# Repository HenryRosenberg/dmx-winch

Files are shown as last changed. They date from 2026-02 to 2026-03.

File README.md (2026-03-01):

# DMX Winch Controller
ESP32-S3–based DMX512 winch controller for theater prop lifting. Supports web configuration, real-time position control, and comprehensive safety features.

**⚠️ For lifting props only. No humans below during movement.**

**These are not comprehensive instructions! This is a project overview**

Roxie Sign Winch v14

<br>

## Resources

| Resource | Link | Notes |
|---|---|---|
| Mechanical CAD Design | [Fusion360](https://a360.co/45cJdRQ) | Current, up-to-date design files |
| Project Overview Drawings | [Roxie Sign Winch Drawing v4](https://github.com/user-attachments/files/25563970/Roxie.Sign.Winch.Drawing.v4.pdf) | Outdated! For reference only. See CAD link for latest design. |
| Electrical Schematics | TBD | Not yet created. Refer to block diagram below |

## Controller Block Diagram
[High Resolution Linked Here](https://github.com/user-attachments/files/25567567/DMX.Winch.Block.Diagram.-.Google.Drawings.pdf)

DMX Winch Block Diagram

<br>

## Controller Parts List

controller_inside
<p align="center">
  
  
</p>

| Component | Part | Notes |
|---|---|---|
| MCU | [ESP32-S3-N16R8](https://www.aliexpress.us/item/3256808865544909.html) + [Carrier Board](https://www.aliexpress.us/item/3256807127113425.html) | Main controller |
| RS485 Transceiver (DMX) | [MAX-485 Module](https://www.aliexpress.us/item/3256809269106959.html) | DMX interface |
| Control PSU | [5V 2A (10W)](https://www.aliexpress.us/item/3256807161025414.html) | Powers MCU + other control circuitry |
| Motor Driver | [DM542T](https://www.omc-stepperonline.com/digital-stepper-driver-1-0-4-2a-20-50vdc-for-nema-17-23-24-stepper-motor-dm542t) | |
| Motor PSU | [48V 5.2A (250W)](https://www.omc-stepperonline.com/250w-48v-5-2a-115-230v-switching-power-supply-stepper-motor-cnc-router-kits-le-250-48) | Not auto-ranging |
| Brake Relay | [3V3 control, 24VDC 1A](https://www.aliexpress.us/item/3256807412441110.html) | |
| Brake PSU | [24V 1A (24W)](https://www.aliexpress.us/item/3256807161025414.html) | |
| Enclosure | [40×30×20 cm fiberglass](https://www.aliexpress.us/item/3256802803154446.html) | Easier to drill/file than steel |
| DIN Rail Mounts | See CAD files | 3D-printed mounts for MCU, relay, PSUs, MAX-485, driver |
| Misc. | WiFi antenna, AC/DC bus bars, PowerCon + 5-pin DMX connectors, panel-mount terminals, enclosure fans + filters, wiring | Source as available |

<br>

## Winch Parts List

Winch_on_floor

| Component | Part | Notes |
|---|---|---|
| Motor | [Dual Shaft NEMA 24 Stepper 4.2A 4Nm](https://www.omc-stepperonline.com/dual-shaft-nema-23-stepper-motor-4-2a-4nm-566oz-in-60x60x100mm-4-wires-24hs39-4204d) | Dual shaft required for brake |
| Electromagnetic Brake | [24V 2.0Nm for NEMA 23/24](https://www.omc-stepperonline.com/dc-electromagnetic-brake-24v-2-0nm-283oz-in-for-nema-23-24-stepper-motor-swb-03) | Failsafe/power loss holding |
| Gearbox | [10:1 Planetary](https://www.omc-stepperonline.com/eg-series-planetary-gearbox-gear-ratio-10-1-backlash-15-arc-min-for-8mm-shaft-nema-23-stepper-motor-eg23-g10-d8) | Low backlash, 8mm input directly from motor |
| Endstop | [ME-8166 Long Arm, N/O](https://www.aliexpress.us/item/3256804700433315.html) | Homing + safety |
| Lifting Drums | [400-12 Garage Door Cable Spools](https://www.amazon.com/dp/B09T5RJZRY) | 4.3" OD 1" ID (use 3d-printed 1/2 shaft adapters) |
| Bearings | [1/2" Bore Pillow Blocks](https://www.amazon.com/dp/B0C61FMWHY) | Self-centering |
| Slip Ring | [1/2" Bore, 6 wire, 10A](https://www.amazon.com/dp/B07XGPVKZK) | Power for light-up props |
| Shaft | [1/2" dia, 6' cold rolled](https://www.mcmaster.com/catalog/4437T11) | |
| Frame | [Engineering Drawing](https://github.com/user-attachments/files/25563765/Roxie.Sign.Winch.Drawing.for.construction.v3.pdf) | 2×4 construction + structural screws |
| Misc. | 14mm×12.7mm shaft coupler, Grade 12.9 hardware, lag bolts, motor mounts | |

<br>

## Engineering Calculations
[Original Calculation Spreadsheet](https://github.com/user-attachments/files/25564224/Chicago.Musical.Sign.Hoist.Calculations.xlsx)

### 1. Mass & Load Estimation (for ROXIE sign)
* **$A$** = $13.5 \text{ ft}^2$ (Area of 3/4" Plywood)
* **$\sigma$** = $2 \text{ lb/ft}^2$ (Density of Plywood)
* **$L$** = $16 \text{ ft}$ (Length of low profile steel Unistrut)
* **$\lambda$** = $0.8 \text{ lb/ft}$ (Linear Density of Low Profile Steel Unistrut)
* **$m_{\text{misc}}$** = $3 \text{ lb}$ (Bulbs & Wiring)

$$m_{\text{est}} = (A \cdot \sigma) + (L \cdot \lambda) + m_{\text{misc}}$$
$$m_{\text{est}} = (13.5 \cdot 2) + (16 \cdot 0.8) + 3 = \mathbf{42.8 \text{ lb}}$$
* **Design Load Limit ($m$):** $\mathbf{50 \text{ lb} \ (22.68 \text{ kg})}$ (before dynamic saftey factors)

---

### 2. Kinematics (Velocity & Gearing)
* **$\Delta y$** = $10 \text{ ft} \ (3.048 \text{ m})$ (Target Lifting Height)
* **$\Delta t$** = $15 \text{ s}$ (Target Lifting Time)
* **$d$** = $3 \text{ in} \ (0.0762 \text{ m})$ (Drum Diameter)
* **$N_{\text{motor}}$** = $500 \text{ RPM}$ (Target Stepper Speed for optimal torque)

**Required Linear Velocity:**
$$v = \frac{\Delta y}{\Delta t} = \frac{3.048}{15} = \mathbf{0.203 \text{ m/s}}$$

**Required Drum RPM:**
$$N_{\text{drum}} = \frac{60 \cdot v}{\pi \cdot d} = \frac{60 \cdot 0.203}{\pi \cdot 0.0762} = \mathbf{50.93 \text{ RPM}}$$

**Required Gear Ratio:**
$$i = \frac{N_{\text{motor}}}{N_{\text{drum}}} = \frac{500}{50.93} = \mathbf{9.82}$$
* **Selected Gearbox:** 10:1 Planetary

---

### 3. Dynamics (Torque & Power)
* **$SF$** = $2$ (Mechanical Safety Factor)
* **$g$** = $9.81 \text{ m/s}^2$
* **$\eta$** = $0.95$ (Gearbox Efficiency)

**Required Drum Torque:**
$$\tau_{\text{drum}} = (m \cdot g \cdot SF) \cdot \frac{d}{2}$$
$$\tau_{\text{drum}} = (22.68 \cdot 9.81 \cdot 2) \cdot \left(\frac{0.0762}{2}\right) = \mathbf{16.95 \text{ Nm}}$$

**Required Motor Torque:**
$$\tau_{\text{motor}} = \frac{\tau_{\text{drum}}}{i \cdot \eta} = \frac{16.95}{10 \cdot 0.95} = \mathbf{1.82 \text{ Nm}}$$
* **Selected Motor:** NEMA 24, Provides 2.2x torque headroom over required

**Required Mechanical Power:**
$$P = \tau_{\text{motor}} \cdot \left( \frac{N_{\text{motor}} \cdot 2\pi}{60} \right)$$
$$P = 1.82 \cdot \left( \frac{500 \cdot 2\pi}{60} \right) = \mathbf{95.16 \text{ W}}$$

---

### 4. Solid Mechanics (Shaft Deflection)
Checking to ensure the 2-foot driveshaft will not bend and bind the pillow block bearings under load. 

* **$E$** = $200 \text{ GPa} \ (2 \times 10^{11} \text{ Pa})$ (Young's Modulus of Steel)
* **$L_{\text{span}}$** = $2 \text{ ft} \ (0.6096 \text{ m})$ (Distance between bearings)
* **$d_{\text{shaft}}$** = $0.5 \text{ in} \ (0.0127 \text{ m})$ (Shaft Diameter)

**Area Moment of Inertia (Solid Circular Shaft):**
$$I = \frac{\pi \cdot d_{\text{shaft}}^4}{64} = \mathbf{1.28 \times 10^{-9} \text{ m}^4}$$

**Maximum Mid-Span Deflection (Worst-case point load assumption):**
$$\delta_{\text{max}} = \frac{F \cdot L_{\text{span}}^3}{48 \cdot E \cdot I}$$
$$\delta_{\text{max}} = \mathbf{0.29 \text{ mm}}$$
* **Conclusion:** Deflection is negligible; shaft is essentially rigid.

---
<br>

# Features

## Motion Control
- Smooth acceleration/deceleration
- Dual-core architecture (Core 0 dedicated to step generation)
- Non-blocking homing with configurable drop distance
- Tick-level position tracking

## DMX
- Single channel (0-255)
- Configurable address (1-512)
- 50ms dropout protection
- Optional auto-home on DMX=0
- Signal loss detection

## Safety
- Emergency stop (power cycle to clear)
- Limit switch monitoring
- Rope loop detection (E-STOP on downward limit hit)
- Auto-recovery (re-home on accidental upward limit hit)
- Electromagnetic brake control

## Web Interface
Screenshot 2026-02-27 at 1 08 30 PM
Access at http://DMXWinch.local if mDNS is supported on the network, else use the IP address assigned by DHCP.

- Real-time position display
- Stroke length, velocity, acceleration adjustment
- Brake modes (stop-on-zero, always-brake, motor-hold)
- Homing configuration
- Manual positioning for setup
- Persistent settings (survives power loss)
- Instant emergency stop button
- Build using the ESP-DASH library

## Status LED (NeoPixel, inside controll cabinet)

- 🔴 Red blink: E-STOP
- 🟣 Purple: Homing
- 🟢 Green: DMX active
- 🟡 Yellow blink: DMX signal lost
- 🟠 Orange: Manual mode
- 🔵 Cyan: Waiting for DMX
- 🔵 Blue: WiFi connecting

## DMX Mapping

- **0**: Auto-home (if enabled)
- **1**: Top (0")
- **255**: Bottomn (max stroke)
- Linear between 1-255

## Homing Sequence

1. Move up until the limit switch
2. Drop configured distance (default 2")
3. Set zero at the drop point
4. Repeat drop if still on limit switch

# Configuration

## Parameters
Edit WiFi in `main.cpp`:
```cpp
const char* ssid = "YourNetwork";
const char* password = "YourPassword";
```
Adjust other parameters in `main.cpp` as needed to match the physical setup.

# Safety Notes

## Automatic E-STOP triggers:
- Limit hit during downward motion (rope loop)
- Manual E-STOP pressed
- Position exceeds 1.5× stroke during homing

## Automatic recovery:
- Limit hit during upward motion (re-homes)
- DMX=0 received (if auto-home enabled)

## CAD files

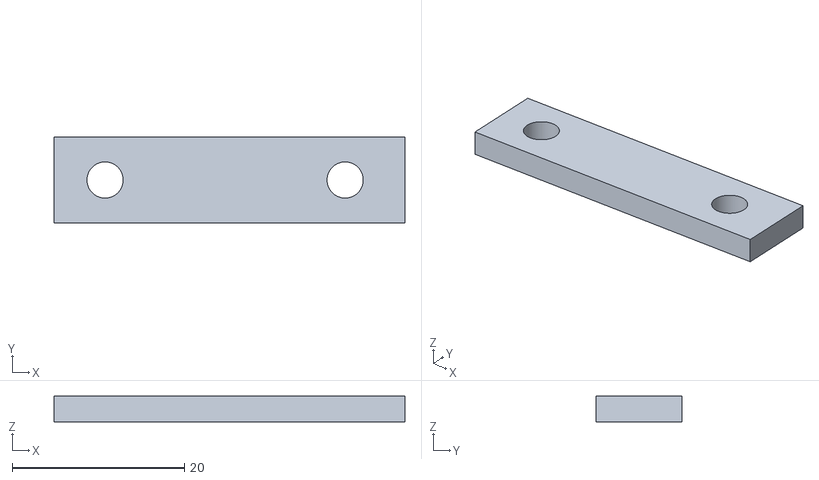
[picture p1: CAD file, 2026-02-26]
Additional STL Files/MAX485-DIN-Top.stl
40.8 x 10.0 x 3.00

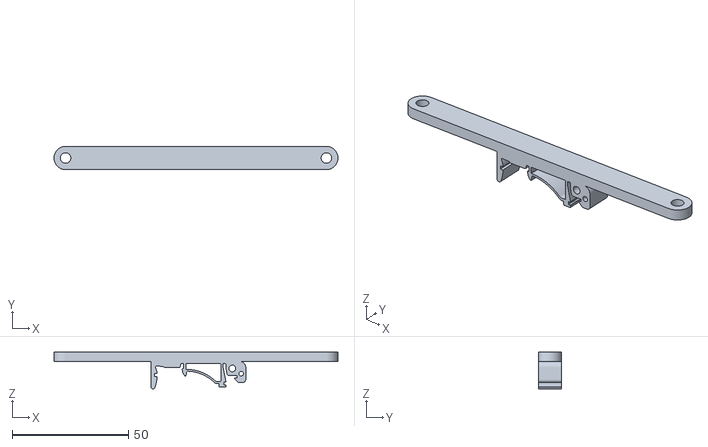
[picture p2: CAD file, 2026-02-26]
Additional STL Files/Driver-DIN-0.75Tolerance.stl
122.0 x 10.0 x 15.8

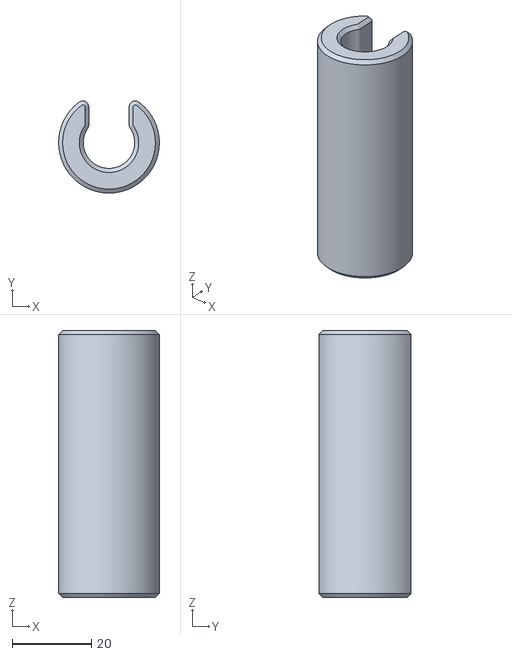
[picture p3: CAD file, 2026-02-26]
Additional STL Files/Garage Door Pulley to 1_2_ Shaft Adapter v1.stl
25.4 x 23.2 x 67.3

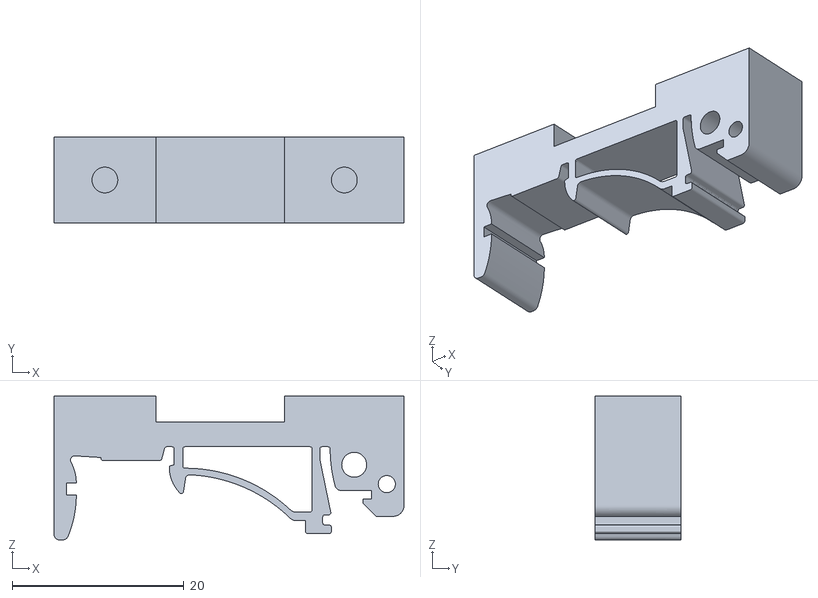
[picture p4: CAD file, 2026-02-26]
Additional STL Files/MAX485-DIN-BASE.stl
40.8 x 10.0 x 16.8

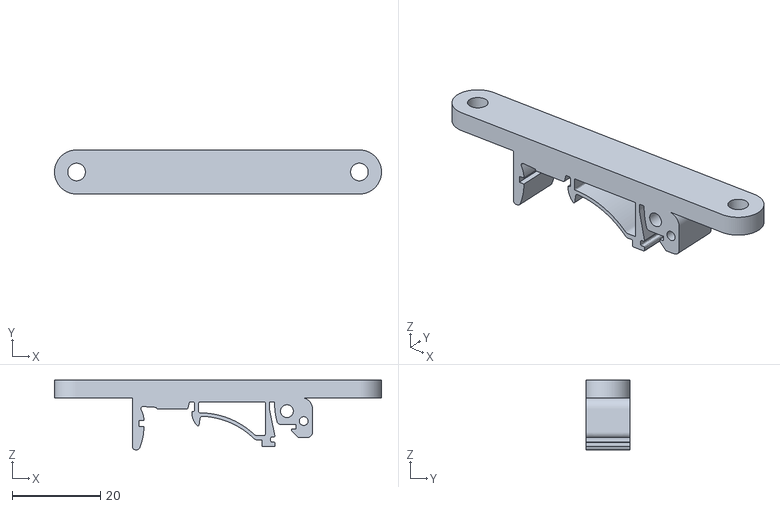
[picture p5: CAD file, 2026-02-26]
Additional STL Files/5V-PSU-DIN.stl
74.0 x 10.0 x 15.8

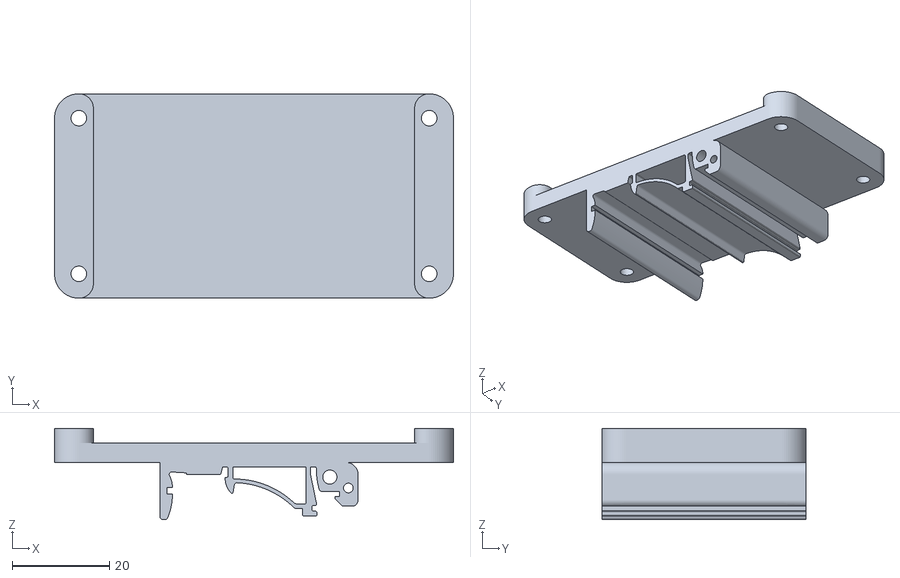
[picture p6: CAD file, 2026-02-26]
Additional STL Files/ESP-DIN.stl
82.0 x 42.0 x 18.8

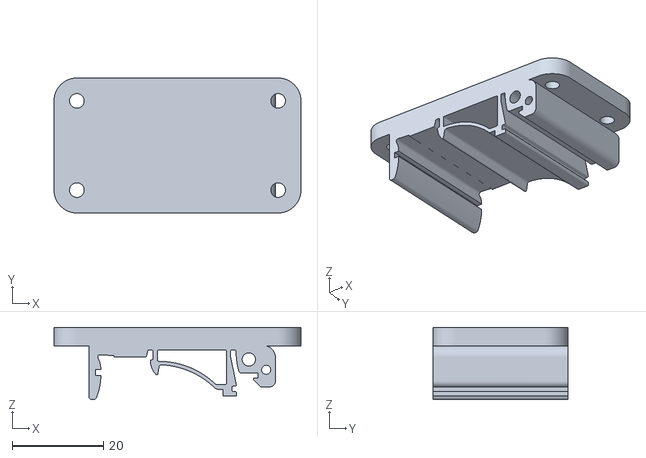
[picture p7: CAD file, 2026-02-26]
Additional STL Files/RELAY-DIN.stl
54.0 x 29.5 x 15.8

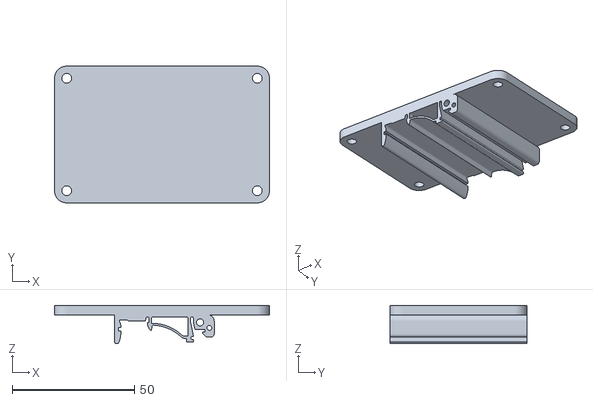
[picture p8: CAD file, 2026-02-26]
Additional STL Files/24V-PSU-DIN.stl
88.0 x 56.0 x 15.8

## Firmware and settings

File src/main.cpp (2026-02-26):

#include <Arduino.h>
#include <WiFi.h>
#include <ESPmDNS.h>
#include <AsyncTCP.h>
#include <ESPAsyncWebServer.h>
#include <ESPDash.h>
#include <AccelStepper.h>
#include <esp_dmx.h>
#include <Preferences.h>
#include <Adafruit_NeoPixel.h>

// WiFi Credentials <------------------------------------------------------- IMPORTANT: WiFi Credentials! <---------
const char* ssid = ""; // Network name
const char* password = ""; // Password
const char* hostname = "DMXWinch";

// DMX Dropout Protection: How long DMX must stay at 0 before acting on it (in milliseconds)
const unsigned long DMX_ZERO_DEBOUNCE_MS = 50; // Adjust this value to filter out momentary dropouts

// Hardware pinouts
const int PIN_STEPPER_PUL = 42;
const int PIN_STEPPER_DIR = 2;
const int PIN_STEPPER_ENA = 1;
const int PIN_STEPPER_BRAKE = 4;
const int PIN_LIMIT_SWITCH = 5;

const int PIN_DMX_RX = 11;  // RO on MAX485
const int PIN_DMX_TX = 14;  // DI on MAX485
const int PIN_DMX_EN = 12;  // DE and RE tied together on MAX485

const int TICKS_PER_REV = 3200;
const int GEAR_RATIO = 10;
const float DRUM_DIA_INCHES = 4.3;
const float INCH_TO_TICKS_RATIO = (GEAR_RATIO * TICKS_PER_REV) / (3.14159 * DRUM_DIA_INCHES);

int winchStrokeLength = 60; // in, Max extension of the winch
float dropDownAfterHoming = 2.0; // in, how much to lower the winch after hitting the endstop
bool autoHomeOnStartup = false; // Auto-home when powered on
bool autoHomeOnDMXZero = false; // Auto-home when DMX value is 0

bool enableDMXControl = true; // Can be disabled via webserver
bool brakeWhenNoMovement = false; // Can be enabled via webserver
bool brakeWhenAtZero = true; // Brake when at home position, can be disabled via webserver
bool isHoming = false; // Flag for non-blocking homing routine
bool homingDropping = false; // Track if we're in the drop-down phase of homing
bool eStopActive = false; // Emergency stop flag
bool dmxInitialized = false; // Track if DMX was successfully initialized

// DMX configuration
int dmxAddress = 1; // DMX start address (1-512)
const dmx_port_t dmxPort = DMX_NUM_1; // Port 0 on ESP32 is used for USB serial
unsigned long lastDmxPacket = 0;
bool dmxEverReceived = false;
const TickType_t DMX_POLL_TICKS = 0; // Non-blocking poll so loop stays responsive

// DMX dropout protection
unsigned long dmxZeroStartTime = 0; // When DMX first went to 0
bool dmxZeroConfirmed = false; // Has DMX been at 0 long enough?

// Persistent storage
Preferences preferences;

// NeoPixel setup
Adafruit_NeoPixel pixel(1, PIN_NEOPIXEL, NEO_GRB + NEO_KHZ800);

// NeoPixel status colors
#define COLOR_OFF             pixel.Color(0,   0,   0)
#define COLOR_WIFI_CONNECTING pixel.Color(0,   0,   100) // Blue
#define COLOR_WIFI_CONNECTED  pixel.Color(0,   100, 100) // Cyan
#define COLOR_DMX_ACTIVE      pixel.Color(0,   100, 0)   // Green
#define COLOR_MANUAL_MODE     pixel.Color(100, 50,  0)   // Orange
#define COLOR_ESTOP           pixel.Color(100, 0,   0)   // Red
#define COLOR_HOMING          pixel.Color(50,  0,   50)  // Purple
#define COLOR_DMX_LOST        pixel.Color(100, 100, 0)   // Yellow

// Use DRIVER mode for PUL/DIR stepper drivers
AccelStepper winchMotor(AccelStepper::DRIVER, PIN_STEPPER_PUL, PIN_STEPPER_DIR);

AsyncWebServer server(80); // Start Webserver
ESPDash dashboard(server); // Attach ESP-DASH to AsyncWebServer

// Webserver widgets
dash::SeparatorCard paramsSeparator(dashboard,              "Parameters:");
dash::SliderCard strokeLengthSlider(dashboard,              "Stroke Length (in)", 0, 240);
dash::SliderCard velocitySlider(dashboard,                  "Max Velocity (in/s)", 0, 20);
dash::SliderCard accelSlider(dashboard,                     "Acceleration (in/s^2)", 0, 50);
dash::ToggleButtonCard brakeWhenNoMovementButton(dashboard, "Brake when stopped?");
dash::ToggleButtonCard brakeWhenAtZeroButton(dashboard,     "Brake when DMX=0?");

dash::SeparatorCard homingSeparator(dashboard,         "Homing Settings:");
dash::SliderCard dropDownSlider(dashboard,             "Drop after homing (in)", 0, 12);
dash::ToggleButtonCard homeButton(dashboard,           "Home now");
dash::ToggleButtonCard autoHomeButton(dashboard,       "Home at startup?");
dash::ToggleButtonCard autoHomeOnZeroButton(dashboard, "Home when DMX=0?");

dash::SeparatorCard dmxSeparator(dashboard,       "DMX Settings:");
dash::ToggleButtonCard enableDMXButton(dashboard, "Enable DMX?");
dash::SliderCard dmxAddressSlider(dashboard,      "DMX Address", 1, 512);
dash::GenericCard dmxStatusCard(dashboard,        "DMX Status:");

dash::SeparatorCard toolsSeparator(dashboard, "Utilities:");
dash::ToggleButtonCard eStopButton(dashboard, "🛑 E-STOP 🛑");
dash::ToggleButtonCard resetButton(dashboard, "Hard Reset");

dash::SeparatorCard manualControlsSeparator(dashboard, "Manual Controls (DMX must be disabled):");
dash::ToggleButtonCard raiseButton(dashboard,          "Raise to 0");
dash::ToggleButtonCard lowerButton(dashboard,          "Lower to max");
dash::SliderCard goToPositionSlider(dashboard,         "Go to position", 0, 240);


void updateNeoPixel() {
  static unsigned long lastBlink = 0;
  static bool blinkState = false;
  
  // Blink every 500ms for certain states
  if(millis() - lastBlink > 500) {
    blinkState = !blinkState;
    lastBlink = millis();
  }
  
  // Priority order of status (highest priority first)
  if(eStopActive) {
    // ESTOP: Blinking red
    pixel.setPixelColor(0, blinkState ? COLOR_ESTOP : COLOR_OFF);
  }
  else if(isHoming) {
    // Homing: Solid purple
    pixel.setPixelColor(0, COLOR_HOMING);
  }
  else if(enableDMXControl && dmxEverReceived && (millis() - lastDmxPacket < 2000)) {
    // DMX Active: Solid green
    pixel.setPixelColor(0, COLOR_DMX_ACTIVE);
  }
  else if(enableDMXControl && dmxEverReceived && (millis() - lastDmxPacket >= 2000)) {
    // DMX Signal Lost: Blinking yellow
    pixel.setPixelColor(0, blinkState ? COLOR_DMX_LOST : COLOR_OFF);
  }
  else if(!enableDMXControl) {
    // Manual Mode: Solid orange
    pixel.setPixelColor(0, COLOR_MANUAL_MODE);
  }
  else if(!dmxInitialized) {
    // DMX init failed: Solid red (dim)
    pixel.setPixelColor(0, COLOR_ESTOP);
  }
  else {
    // WiFi Connected, waiting for DMX: Solid cyan
    pixel.setPixelColor(0, COLOR_WIFI_CONNECTED);
  }
  
  pixel.show();
}

// Motor task - runs on Core 0 for maximum smoothness
void motorTask(void* parameter) {
  // Disable watchdog for this task
  disableCore0WDT();
  
  while(true) {
    winchMotor.run();
  }
}

void setup() {
  Serial.begin(115200);
  Serial.println("\n\n=== DMX Winch Controller Starting ===");

  // Initialize NeoPixel
  pixel.begin();
  pixel.setBrightness(50); // 0-255
  pixel.setPixelColor(0, COLOR_WIFI_CONNECTING); // Blue while connecting
  pixel.show();

  pinMode(PIN_STEPPER_PUL,   OUTPUT);
  pinMode(PIN_STEPPER_DIR,   OUTPUT);
  pinMode(PIN_STEPPER_ENA,   OUTPUT);
  pinMode(PIN_STEPPER_BRAKE, OUTPUT);
  pinMode(PIN_LIMIT_SWITCH,  INPUT_PULLDOWN);
  
  digitalWrite(PIN_STEPPER_ENA, HIGH); // Disable the stepper driver on startup
  digitalWrite(PIN_STEPPER_BRAKE, LOW); // Engage brake on startup

  // Load persistent settings
  preferences.begin("winch", false); // Open in read/write mode
  winchStrokeLength = preferences.getInt("strokeLength", 60);
  brakeWhenNoMovement = preferences.getBool("brakeWhenStop", false);
  brakeWhenAtZero = preferences.getBool("brakeAtZero", true);
  dmxAddress = preferences.getInt("dmxAddress", 1);
  enableDMXControl = preferences.getBool("enableDMX", true);
  dropDownAfterHoming = preferences.getFloat("dropDown", 2.0);
  autoHomeOnStartup = preferences.getBool("autoHome", false);
  autoHomeOnDMXZero = preferences.getBool("autoHomeDMX0", false);
  
  Serial.println("Loaded persistent settings:");
  Serial.print("  Stroke Length: "); Serial.println(winchStrokeLength);
  Serial.print("  Drop After Homing: "); Serial.println(dropDownAfterHoming);
  Serial.print("  Auto Home (Startup): "); Serial.println(autoHomeOnStartup ? "Yes" : "No");
  Serial.print("  Auto Home (DMX=0): "); Serial.println(autoHomeOnDMXZero ? "Yes" : "No");
  Serial.print("  DMX Zero Debounce: "); Serial.print(DMX_ZERO_DEBOUNCE_MS); Serial.println(" ms");
  Serial.print("  DMX Address: "); Serial.println(dmxAddress);
  Serial.print("  Enable DMX: "); Serial.println(enableDMXControl ? "Yes" : "No");
  Serial.print("  INCH_TO_TICKS_RATIO: "); Serial.println(INCH_TO_TICKS_RATIO);

  // Configure DMX (esp_dmx returns bool: true = success)
  Serial.println("Initializing DMX...");
  dmx_config_t config = DMX_CONFIG_DEFAULT;
  dmx_personality_t personalities[] = {
    {1, "Winch Position"} // 1 channel personality
  };
  int personality_count = 1;

  if (dmx_driver_install(dmxPort, &config, personalities, personality_count)) {
    Serial.println("DMX driver installed");
    if (dmx_set_pin(dmxPort, PIN_DMX_TX, PIN_DMX_RX, PIN_DMX_EN)) {
      Serial.println("DMX pins configured");
      dmxInitialized = true;
      Serial.println("DMX initialized on port 1");
      Serial.print("Listening on DMX address: ");
      Serial.println(dmxAddress);
    } else {
      Serial.println("ERROR: Failed to set DMX pins");
    }
  } else {
    Serial.println("ERROR: Failed to install DMX driver");
  }

  // Connect to WiFi
  WiFi.mode(WIFI_STA);
  WiFi.begin(ssid, password);
  if (WiFi.waitForConnectResult() != WL_CONNECTED) {
      Serial.printf("WiFi Failed!\n");
      return;
  }
  Serial.print("IP Address: ");
  Serial.println(WiFi.localIP());
  Serial.print("RSSI: ");
  Serial.println(WiFi.RSSI());

  // mDNS allows the webpage to appear on http://DMXWinch.local
  if (!MDNS.begin(hostname)) {
    Serial.println("Error setting up MDNS");
  } else {
    Serial.print("mDNS started. Connect to: http://");
    Serial.print(hostname);
    Serial.println(".local");
  }

  WiFi.setAutoReconnect(true); // Automatically reconenct to WiFi if disconnected

  // Webserver callback configuration ---------------------------------------------
  enableDMXButton.onChange([](bool state){
    Serial.println(String("Enable DMX: ")+(state?"true":"false"));
    
    enableDMXControl = state;
    preferences.putBool("enableDMX", state);
    
    if (state) {
      dmxEverReceived = false;
      lastDmxPacket = 0;
      Serial.println("DMX state reset - ready for first packet");
    }

    enableDMXButton.setValue(state);
    dashboard.sendUpdates();
  });
  
  brakeWhenNoMovementButton.onChange([](bool state){
    Serial.println(String("Brake When No Movement: ")+(state?"true":"false"));
    
    brakeWhenNoMovement = state;
    preferences.putBool("brakeWhenStop", state);

    brakeWhenNoMovementButton.setValue(state);
    dashboard.sendUpdates();
  });

  brakeWhenAtZeroButton.onChange([](bool state){
    Serial.println(String("Brake When At Zero: ")+(state?"true":"false"));
    
    brakeWhenAtZero = state;
    preferences.putBool("brakeAtZero", state);

    brakeWhenAtZeroButton.setValue(state);
    dashboard.sendUpdates();
  });

  dropDownSlider.onChange([](int value){
    Serial.println("Drop Down Slider Triggered: "+String(value));
    
    dropDownAfterHoming = (float)value;
    preferences.putFloat("dropDown", dropDownAfterHoming);
    
    dropDownSlider.setValue(value);
    dashboard.sendUpdates();
  });

  autoHomeButton.onChange([](bool state){
    Serial.println(String("Auto Home on Startup: ")+(state?"true":"false"));
    
    autoHomeOnStartup = state;
    preferences.putBool("autoHome", state);

    autoHomeButton.setValue(state);
    dashboard.sendUpdates();
  });

  autoHomeOnZeroButton.onChange([](bool state){
    Serial.println(String("Auto Home on DMX=0: ")+(state?"true":"false"));
    
    autoHomeOnDMXZero = state;
    preferences.putBool("autoHomeDMX0", state);

    autoHomeOnZeroButton.setValue(state);
    dashboard.sendUpdates();
  });

  homeButton.onChange([](bool state){
    if(eStopActive) {
      Serial.println("ESTOP ACTIVE - Cannot home");
      return;
    }
    
    Serial.println("Home Button Triggered - Starting homing routine");
    
    if(state) {
      homingDropping = false; // Reset the homing state
      isHoming = true; // Start non-blocking homing routine
    }
  });

  eStopButton.onChange([](bool state){
    if(state) {
      Serial.println("🛑 EMERGENCY STOP ACTIVATED! 🛑");
      eStopActive = true;
      
      // Stop motor immediately
      winchMotor.stop();
      winchMotor.setCurrentPosition(winchMotor.currentPosition()); // Hold position
      
      // Engage brake and disable motor
      digitalWrite(PIN_STEPPER_BRAKE, LOW);
      digitalWrite(PIN_STEPPER_ENA, HIGH);
      
      // Disable DMX
      enableDMXControl = false;
      
      // Stop homing if active
      isHoming = false;
      
      eStopButton.setValue(true);
      dashboard.sendUpdates();
    }
  });

  resetButton.onChange([](bool state){
    Serial.println("Hard Reset Button Triggered");
    
    if(state) {
      // Engage brake and enable stepper driver during reset
      digitalWrite(PIN_STEPPER_BRAKE, LOW); // Enable motor brake
      digitalWrite(PIN_STEPPER_ENA, LOW); // Enable stepper driver
      
      delay(50); // Brief delay to ensure brake engages
      
      ESP.restart(); // Restart the MCU
    }
  });
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
void loop() {
  // Update NeoPixel status (quick, non-blocking)
  updateNeoPixel();
  
  // ESTOP overrides everything
  if(eStopActive) {
    digitalWrite(PIN_STEPPER_BRAKE, LOW);  // Brake engaged
    digitalWrite(PIN_STEPPER_ENA, HIGH);   // Motor disabled
    
    static unsigned long lastEStopMsg = 0;
    if(millis() - lastEStopMsg > 5000) {
      Serial.println("🛑 ESTOP ACTIVE 🛑 Cycle power to continue");
      if(WiFi.isConnected()) {
        dmxStatusCard.setValue("🛑 ESTOP ACTIVE 🛑");
        dashboard.sendUpdates();
      }
      lastEStopMsg = millis();
    }
    return;
  }

  // Limit switch: reset position if at home and motor thinks it's below zero
  bool limitSwitchTriggered = (analogReadMilliVolts(PIN_LIMIT_SWITCH) > 2500);
  if (limitSwitchTriggered && winchMotor.currentPosition() < 0 && !isHoming) {
    Serial.println("SAFETY: Limit switch hit while below zero - resetting to 0");
    winchMotor.setCurrentPosition(0);
    winchMotor.moveTo(0);
  }

  // Non-blocking homing routine
  if (isHoming) {
    digitalWrite(PIN_STEPPER_BRAKE, HIGH);
    digitalWrite(PIN_STEPPER_ENA, LOW);
    
    if (!homingDropping && limitSwitchTriggered) {
      // Step 1: Hit limit switch, now drop down
      Serial.print("Limit switch hit - dropping down ");
      Serial.print(dropDownAfterHoming);
      Serial.println("\"...");
      winchMotor.setCurrentPosition(0); // Current position is now zero
      winchMotor.moveTo(dropDownAfterHoming * INCH_TO_TICKS_RATIO); // Move down by dropDown amount
      homingDropping = true;
    } 
    else if (homingDropping && !winchMotor.isRunning()) {
      // Step 2: Finished dropping, check if still on limit switch
      if(limitSwitchTriggered) {
        // Still on limit switch after dropping - need to drop more!
        Serial.println("Still on limit switch after drop - dropping another " + String(dropDownAfterHoming) + "\"");
        winchMotor.setCurrentPosition(0);
        winchMotor.moveTo(dropDownAfterHoming * INCH_TO_TICKS_RATIO);
        // Stay in homingDropping mode
      } else {
        // Successfully dropped off limit switch - complete homing
        Serial.println("Drop complete - setting new zero");
        winchMotor.setCurrentPosition(0); // This dropped position is now the new zero
        winchMotor.moveTo(0); // Target is zero (stay here)
        isHoming = false;
        homingDropping = false;
        Serial.println("*** HOMING COMPLETE ***");
      }
    } 
    else if (!homingDropping) {
      // Step 0: Still searching for limit switch
      winchMotor.moveTo(-100000);
      
      // Safety check: if motor has moved too far, abort homing
      if(winchMotor.currentPosition() <= -1.5 * winchStrokeLength * INCH_TO_TICKS_RATIO) {
        isHoming = false;
        homingDropping = false;
        Serial.println("HOMING ABORTED - Extension limit reached without hitting limit switch");
        winchMotor.setCurrentPosition(0);
        winchMotor.moveTo(0);
      }
    }
    return;
  }

  // DMX Control - FAST, non-blocking poll
  static uint8_t lastDmxValue = 255;  // Track last value to avoid redundant moveTo calls
  if (enableDMXControl && dmxInitialized) {
    dmx_packet_t packet;
    size_t slotsNeeded = (size_t)(dmxAddress + 1);
    size_t received = dmx_receive_num(dmxPort, &packet, slotsNeeded, DMX_POLL_TICKS);

    if (received && !packet.err && packet.size > (size_t)dmxAddress) {
      int slotValue = dmx_read_slot(dmxPort, dmxAddress);
      if (slotValue >= 0) {
        uint8_t dmxValue = (uint8_t)slotValue;
        
        // DROPOUT PROTECTION: Special handling for DMX = 0
        if(dmxValue == 0) {
          if(dmxZeroStartTime == 0) {
            // First time we've seen 0 - start the timer
            dmxZeroStartTime = millis();
            dmxZeroConfirmed = false;
          } else if(!dmxZeroConfirmed && (millis() - dmxZeroStartTime >= DMX_ZERO_DEBOUNCE_MS)) {
            // DMX has been at 0 for long enough - confirm it
            dmxZeroConfirmed = true;
            Serial.print("DMX=0 confirmed after ");
            Serial.print(DMX_ZERO_DEBOUNCE_MS);
            Serial.println("ms");
          }
        } else {
          // DMX is not 0 - reset the zero detection
          dmxZeroStartTime = 0;
          dmxZeroConfirmed = false;
        }
        
        // Only update position if DMX value changed AND if it's 0, it must be confirmed
        if(dmxValue != lastDmxValue) {
          if (!dmxEverReceived) {
            Serial.println("*** FIRST DMX PACKET RECEIVED! ***");
            dmxEverReceived = true;
          }
          
          // DMX = 0: Only act on it if confirmed (not a momentary dropout)
          if(dmxValue == 0) {
            if(dmxZeroConfirmed && autoHomeOnDMXZero) {
              Serial.println("DMX: Ch" + String(dmxAddress) + " = 0 (confirmed) → Starting auto-home");
              homingDropping = false; // Reset the homing state
              isHoming = true;
              lastDmxValue = dmxValue; // Update so we don't repeat
            }
            // If not confirmed yet, don't update lastDmxValue - wait for confirmation
          }
          else {
            // DMX 1-255: Map to stroke length (1 goes to top, 255 goes to max)
            int targetPosition = map(dmxValue, 1, 255, 0, winchStrokeLength);
            Serial.print("DMX: Ch");
            Serial.print(dmxAddress);
            Serial.print(" = ");
            Serial.print(dmxValue);
            Serial.print(" → Moving to ");
            Serial.print(targetPosition);
            Serial.println("\"");
            
            winchMotor.moveTo(targetPosition * INCH_TO_TICKS_RATIO);
            lastDmxValue = dmxValue;
          }
        }
        
        lastDmxPacket = millis();
      }
    }
  }


  // Brake and motor enable control  
  if(winchMotor.isRunning()) {
    digitalWrite(PIN_STEPPER_BRAKE, HIGH);
    digitalWrite(PIN_STEPPER_ENA, LOW);
  }
  else if(brakeWhenAtZero && winchMotor.currentPosition() == 0) {
    digitalWrite(PIN_STEPPER_BRAKE, LOW);
    digitalWrite(PIN_STEPPER_ENA, HIGH);
  }
  else if(brakeWhenNoMovement) {
    digitalWrite(PIN_STEPPER_BRAKE, LOW);
    digitalWrite(PIN_STEPPER_ENA, HIGH);
  }
  else {
    digitalWrite(PIN_STEPPER_BRAKE, HIGH);
    digitalWrite(PIN_STEPPER_ENA, LOW);
  }

  // Limit switch safety - CRITICAL: Detects problems!
  // Only check if NOT homing (homing handles its own limit switch logic)
  if (limitSwitchTriggered && !isHoming) {
    int currentPos = winchMotor.currentPosition();
    int targetPos = winchMotor.targetPosition();
    
    // Moving upward (target < current): Normal - trigger homing with drop
    if (targetPos < currentPos) {
      Serial.println("SAFETY: Limit switch hit during upward movement - starting homing with drop");
      winchMotor.stop();
      homingDropping = false; // Reset state for fresh homing
      isHoming = true; // This will trigger the full homing routine with drop
    }
    // Moving downward (target > current): PROBLEM - rope may be looped!
    else if (targetPos > currentPos) {
      Serial.println("🚨 CRITICAL ERROR: Limit switch hit during DOWNWARD movement!");
      Serial.println("🚨 This likely means the rope has looped around the drum!");
      Serial.println("🚨 Triggering E-STOP for safety");
      
      eStopActive = true;
      winchMotor.stop();
      digitalWrite(PIN_STEPPER_BRAKE, LOW);
      digitalWrite(PIN_STEPPER_ENA, HIGH);
      enableDMXControl = false;
      
      if(WiFi.isConnected()) {
        dmxStatusCard.setValue("🚨 ROPE LOOP ERROR 🚨");
        eStopButton.setValue(true);
        dashboard.sendUpdates();
      }
    }
  }

  // PERIODIC UPDATES (non-critical, every 1/4 second), only do if WiFi is connected
  static unsigned long lastPeriodicUpdate = 0;
  if((millis() - lastPeriodicUpdate > 250) && WiFi.isConnected()) {
    lastPeriodicUpdate = millis();
    
    // Update dashboard based on current mode
    if(enableDMXControl && dmxInitialized) {
      if(dmxEverReceived && (millis() - lastDmxPacket < 2000)) {
        int currentPos = winchMotor.targetPosition() / INCH_TO_TICKS_RATIO;
        dmxStatusCard.setValue(String("DMX: ") + String(lastDmxValue) + " → " + String(currentPos) + "\"");
      } else if(dmxEverReceived) {
        dmxStatusCard.setValue("DMX Signal Lost");
      } else {
        dmxStatusCard.setValue("Waiting for DMX...");
      }
      dashboard.sendUpdates();
    } else if(!enableDMXControl) {
      dmxStatusCard.setValue("Manual Control");
      dashboard.sendUpdates();
    } else {
      dmxStatusCard.setValue("DMX Init Failed");
      dashboard.sendUpdates();
    }
  }
}
